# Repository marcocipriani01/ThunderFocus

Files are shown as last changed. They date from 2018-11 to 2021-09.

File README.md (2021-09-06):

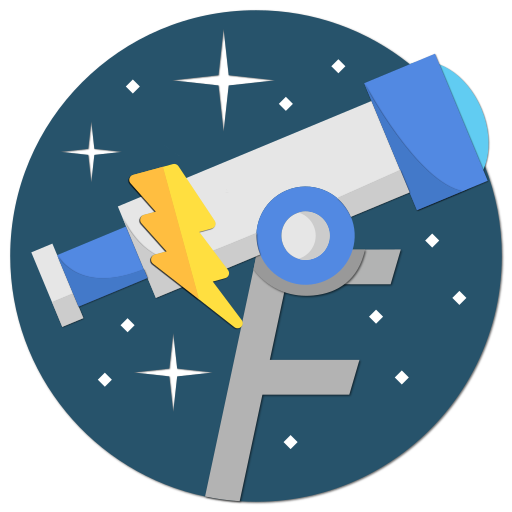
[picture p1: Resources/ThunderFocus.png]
ThunderFocus logo


# ThunderFocus

ThunderFocus is an open-source telescope focuser developed by Marco Cipriani. The source code is available on [GitHub](https://github.com/marcocipriani01/ThunderFocus) and is issued under the [GNU General Public License version 3](https://www.gnu.org/licenses/gpl-3.0.html). By using this software, you accept all the terms of its license.

## Showcase of controllers and focusers [on my website](https://marcocipriani01.github.io/projects/ThunderFocus)!

## Description of the project

ThunderFocus is an all-in-one focuser and power box (dew heater controller) designed to be fully customizable and feature-rich. It has its own control software written in Java and is both [INDI](https://indilib.org/) and [ASCOM](https://ascom-standards.org/) compatible.

The firmware can run on both Arduino and Teensy, with the only difference being the RTC support and the speed of the MCU. Thanks to the firmware configuration file, you can select only the features you need and remove the unnecessary: the control software will detect the available features and display only the options supported by the board, so you won't need to modify other files.

The user interface is platform-independent and works seamless across computers and boards like Raspberry Pi, with the only requirement being Java 15 (bundled in the Windows installer): in this way, you get the same experience no matter what OS you run. Moreover, it uses [INDIForJava](http://indiforjava.sourceforge.net/stage/index.html) for INDI/KStars compatibility and a special ASCOM driver for Windows compatibility. As a bonus, it can also be controlled using the [IPARCOS Android app](https://marcocipriani01.github.io/projects/IPARCOS) when the INDI server is enabled!

## Features

- INDI/ASCOM compatibility, cross platform interface
- Full telescope focuser control
  - Can control either one main telescope focuser or one guidescope/off-axis guider focuser
  - Backlash compensation
  - Precise micro-stepping control for pin-point stars
  - Displays the focuser position in millimeters, ticks or any unit of your liking
  - Remembers the last position
- Advanced dew heaters control, which can also turn on and off the telescope mount or other accessories.
  - Various automatic modes: temperature, dew point, humidity, sunset/sunrise
  - Manual control/override of outputs
  - Completely autonomous after configuration: can work without a PC
  - Restores the last state after power up
  - High efficiency, does not require heatsinks or cooling
- Ambient monitoring
  - Temperature, humidity, dew point
  - Graphs of the whole observing night

## Contributing to the project

I really appreciate help, feel free to fork, open issues, start pull requests...

## Installing the software

### Windows x64

Get [the latest release](https://github.com/marcocipriani01/ThunderFocus/releases) and install it. You're done!

### Debian, Ubuntu and Raspberry Pi OS

**Skip the Java installation if you already have it installed!**

Install the latest Java Development Kit available, version 16 or greater. On Ubuntu:

- `sudo apt update`
- `sudo apt install openjdk-16-jdk`

Raspberry Pi OS or Astroberry:

- Download the latest [AdoptOpenJDK](https://adoptopenjdk.net/releases.html) JRE or JDK (recommended: version 16, HotSpot JVM)
- Run `sudo mkdir /usr/java/`
- Extract the archive: `sudo tar -zxf AdoptOpenJDK.tar -C /usr/java/` (change the filename accordingly to what you downloaded)
- Run `echo 'export PATH=$PATH:/usr/java/' | sudo tee -a /etc/profile`

### macOS, Windows 32-bit and other Linux distros

Install Java version 15 or greater depending on your OS and then use the `.jar` ThunderFocus release. Someday I will add a macOS installer...

## Using the control software

Coming soon...

## The electronics

I created several circuits for ThunderFocus, all sharing more or less the same functionalities:

1. The prototype I use on my own telescope (not in this repository).
2. A Teensy 4 "overkill" board, with RTC and dual focuser support, not yet implemented in software. The PCB also includes a flip-flap circuit for [my other project](https://github.com/marcocipriani01/ArduinoFlatBox).
3. The **recommended Arduino Nano PCB**, which supports:
   - One focuser (bipolar motor)
   - Hand controller
   - Two PWM outputs and one digital for dew heaters and telescope mount power (with relay) respectively.
   - I2C RTC clock predisposition, to be implemented in software
   - Protection against over-current and reverse polarity

If you want to replicate this project, please build the third PCB. You can use the included CAM job to generate the gerber files and order them using services like [JLCPCB](https://jlcpcb.com/). The board is designed to be cut (following a line on the silkscreen) if you don't want the output controller: in this way, you can order 5 identical PCBs (the minimum on JLCPCB) and choose which one to cut and which not to. Maybe give the remaining boards to your friends and avoid wastes!

Building the board is an easy job, just add the components you see in the schematics. For reference, here's the list of what you need:

| Number | Component |
|---|:---:|
| C1 |  100uF electrolytic capacitor |
| C2 | 0.33uF electrolytic capacitor |
| C3 |  0.1uF electrolytic capacitor |
| C4 |  47uF electrolytic capacitor  |
| C5 |  100uF electrolytic capacitor |
| CNx |  2.1x5.5mm barrel plug socket |
| D1 | 1N4004 diode |
| D2 | 1N4004 diode |
| DRV1 | DRV8825 stepper driver |
| F1 | 5x20 fuse holder |
| IC1 | LM7805 linear regulator |
| J2 | RJ11/RJ12 female connector  |
| K1 | 12V relay |
| LED1 | 5mm red LED |
| Q2 | IRF540 N-channel MOSFET |
| Q3 | IRF540 N-channel MOSFET |
| Q5 | BC547 NPN transistor |
| R1 | 330 ohm resistor |
| R2 | 1K resistor |
| R3 | 4.7K resistor |
| R4 | 4.7K resistor |
| R5 | 10K resistor |
| U1 | Arduino Nano board |

## 3D-printed brackets

At the moment, the only bracket in the repository is for the Sky-Watcher 200 f/5 newtonian (2017 model, newer ones may be different) and uses a circular connector. I'm looking forward to add new 3D models with the right connector - the RJ11. Feel free to submit yours using pull requests!

## The stepper motor

The firmware is pretty much motor/driver-agnostic. Just make sure to select the right driver type in the configuration files (`DRIVER_POLOLU` if you're using the Arduino Nano PCB). On my newtonian OTA, which has a crayford focuser and only moves a DSLR, I'm using a small NEMA 11 stepper motor. My recommendation is to use a geared (1:4 ~ 1:14) stepper if you're attaching the motor directly to the focuser axis or a direct stepper if on the knob of a dual-speed focuser. Use properly sized timing belt and pulley or a shaft coupler to connect the motor to the focuser.

## Development

### Building the firmware

1. Install [Visual Studio Code](https://code.visualstudio.com/) and the [PlatformIO](https://platformio.org/install/ide?install=vscode) extension
2. Install the Arduino or Teensy core in the PlatformIO boards manager
3. Open the `ThunderFocus-firmware` folder inside VS Code
4. Select the PlatformIO Project Environment (`nanoatmega328` or `teensy40`) from the status bar, or add a custom one in `platformio.ini`
5. Open `src/config.h` and enable **one and only one** of the following lines (according to the PCB you built):
   - `#include "boards/arduino_nano_pcb.h"`
   - `#include "boards/teensy_max_pcb.h"`
6. Open the configuration file you enabled and make the appropriate changes (comments in the file will guide you)
   - Select the pins according to your circuit
   - Enable or disable features
   - Eventual errors or incompatible combinations of features will stop the compilation
7. Done! Upload the firmware

### Building the control software `jar` files

1. Install a [Java Development Kit](https://www.oracle.com/java/technologies/javase-downloads.html), version 15 or greater
2. Install [IntelliJ IDEA community](https://www.jetbrains.com/idea/)
3. Open `ThunderFocus-GUI` inside IntelliJ
4. Just run the only configuration in the project, it will build the artifacts for you and place them in the right places

### Creating the Windows installer

Requires the `jar` files. Make sure to follow the previous step.

1. Install [Inno Setup](https://jrsoftware.org/isinfo.php) and [Visual Studio](https://visualstudio.microsoft.com/it/) with Visual Basic .NET support
2. Open `ThunderFocusASCOM` inside Visual Studio
3. Compile the _Release_ configuration (do not run it)
4. Extract a copy of the [AdoptOpenJDK](https://adoptopenjdk.net/releases.html) in the `JRE-bundle` folder
    - Recommended: _OpenJDK 15_ with _HotSpot VM_, Windows x64
5. Open `InnoSetup.iss` and make the necessary changes to the file:
    - Replace `D:\ThunderFocus\` with the path to the ThunderFocus repository in your computer
6. Compile and run the Inno Setup file: it will create the Windows installer in the `Installers` folder

### Creating the Debian package

Requires the `jar` files and a Debian installation with `dpkg-deb`. Note: the Debian package will not include a bundled JDK. Make sure to install it and make the necessary changes to the `PATH` env variable.

1. Run `cd ThunderFocus-GUI/deb-builder`
2. `./build.sh` (requires `root` access to set the appropriate permissions)
3. You're done, the installer will be located in the usual `Installers` folder

## Used libraries

- [OpenJDK 15](https://openjdk.java.net/) by Oracle, [GPL v2 license with linking exception](https://openjdk.java.net/legal/gplv2+ce.html)
- [AdoptOpenJDK builds](https://adoptopenjdk.net/index.html) with HotSpot VM, by AdoptOpenJDK, [Apache 2.0 license](https://www.apache.org/licenses/LICENSE-2.0.html)
- [INDIForJava](https://indiforjava.github.io/) by Marco Cipriani, Sergio Alonso and Richard van Nieuwenhoven, [LGPL v3 license](https://github.com/INDIForJava/INDIForJava-core/blob/main/LICENSE.txt)
- [ASCOM .NET libraries](https://www.ascom-standards.org/) by The ASCOM Initiative, [ASCOM Open Source License](https://github.com/ASCOMInitiative/ASCOMPlatform/blob/master/LICENSE.txt)
- [jssc](https://github.com/java-native/jssc) by java-native and scream3r, [LGPL v3 license](https://github.com/java-native/jssc/blob/master/LICENSE.txt)
- [FlatLaf](https://github.com/JFormDesigner/FlatLaf/) by JFormDesigner, [Apache 2.0 license](https://github.com/JFormDesigner/FlatLaf/blob/master/LICENSE)
- [Gson](https://github.com/google/gson) by Google, [Apache 2.0 license](https://github.com/google/gson/blob/master/LICENSE)
- [Material icons](https://material.io/resources/icons/) by Google, [Apache 2.0 license](https://www.apache.org/licenses/LICENSE-2.0.html)
- [Arduino Core APIs](https://github.com/arduino/Arduino) by Arduino, [LGPL v3 license](https://github.com/arduino/Arduino/blob/master/license.txt)
- [AccelStepper](https://www.airspayce.com/mikem/arduino/AccelStepper/) by Mike McCauley (with modifications), [GPL v3 license](https://www.gnu.org/licenses/gpl-3.0.html)
- [Arduino Time Library](https://github.com/PaulStoffregen/Time) by Michael Margolis, [LGPL v2.1 license](https://www.gnu.org/licenses/old-licenses/lgpl-2.1.html)
- [SolarPosition library](https://github.com/KenWillmott/SolarPosition) by Ken Willmott
  - Based on [_Arduino Uno and Solar Position Calculations_](http://www.instesre.org/ArduinoDocuments.htm), © David R. Brooks, issued under the [Creative Commons Attribution-NonCommercial-NoDerivatives 4.0 International License](https://creativecommons.org/licenses/by-nc-nd/4.0/)
  - Uses equations from the book [_Astronomical Algorithms_ by Jean Meeus](https://www.willbell.com/math/mc1.HTM), published by Willmann-Bell, Inc., Richmond, VA
- [DHT sensor library](https://github.com/adafruit/DHT-sensor-library) by Adafruit, [MIT license](https://github.com/adafruit/DHT-sensor-library/blob/master/license.txt)
- [Telescope icon](https://www.flaticon.com/free-icon/telescope_547425?term=telescope&page=1&position=9&related_item_id=547425) by Freepik, [Flaticon license](https://www.freepikcompany.com/legal#nav-flaticon)

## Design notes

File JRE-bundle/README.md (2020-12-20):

ThunderFocus logo

# ThunderFocus

ThunderFocus is an open-source telescope focuser developed by Marco Cipriani. It has its own contorl software written in Java, can be integrated into an [INDI](https://indilib.org/) server and has an ASCOM driver. The source code is available on [GitHub](https://github.com/marcocipriani01/ThunderFocus) and is issued under the [GNU General Public License version 3](https://www.gnu.org/licenses/gpl-3.0.html). By using this software, you accept all the terms of its license.

## Used libraries

- [OpenJDK 14](https://openjdk.java.net/) by Oracle, [GPL v2 license with linking exception](https://openjdk.java.net/legal/gplv2+ce.html)
- [AdoptOpenJDK builds](https://adoptopenjdk.net/index.html) with HotSpot VM, by AdoptOpenJDK, [Apache 2.0 license](https://www.apache.org/licenses/LICENSE-2.0.html)
- [INDIForJava](http://indiforjava.sourceforge.net/stage/index.html) by Sergio Alonso and Richard van Nieuwenhoven, [LGPL v3 license](http://indiforjava.sourceforge.net/stage/license.html)
- [ASCOM .NET libraries](https://www.ascom-standards.org/) by The ASCOM Initiative, [ASCOM Open Source License](https://github.com/ASCOMInitiative/ASCOMPlatform/blob/master/LICENSE.txt)
- [jssc](https://github.com/java-native/jssc) by java-native and scream3r, [LGPL v3 license](https://github.com/java-native/jssc/blob/master/LICENSE.txt)
- [FlatLaf](https://github.com/JFormDesigner/FlatLaf/) by JFormDesigner, [Apache 2.0 license](https://github.com/JFormDesigner/FlatLaf/blob/master/LICENSE)
- [Gson](https://github.com/google/gson) by Google, [Apache 2.0 license](https://github.com/google/gson/blob/master/LICENSE)
- [Material icons](https://material.io/resources/icons/) by Google, [Apache 2.0 license](https://www.apache.org/licenses/LICENSE-2.0.html)
- [Arduino Core APIs](https://github.com/arduino/Arduino) by Arduino, [LGPL v3 license](https://github.com/arduino/Arduino/blob/master/license.txt)
- [AccelStepper](https://www.airspayce.com/mikem/arduino/AccelStepper/) by Mike McCauley (with modifications), [GPL v3 license](https://www.gnu.org/licenses/gpl-3.0.html)
- [Arduino Time Library](https://github.com/PaulStoffregen/Time) by Michael Margolis, [LGPL v2.1 license](https://www.gnu.org/licenses/old-licenses/lgpl-2.1.html)
- [SolarPosition library](https://github.com/KenWillmott/SolarPosition) by Ken Willmott
  - Based on [_Arduino Uno and Solar Position Calculations_](http://www.instesre.org/ArduinoDocuments.htm), © David R. Brooks, issued under the [Creative Commons Attribution-NonCommercial-NoDerivatives 4.0 International License](https://creativecommons.org/licenses/by-nc-nd/4.0/)
  - Uses equations from the book [_Astronomical Algorithms_ by Jean Meeus](https://www.willbell.com/math/mc1.HTM), published by Willmann-Bell, Inc., Richmond, VA
- [DHT sensor library](https://github.com/adafruit/DHT-sensor-library) by Adafruit, [MIT license](https://github.com/adafruit/DHT-sensor-library/blob/master/license.txt)
- [Telescope icon](https://www.flaticon.com/free-icon/telescope_547425?term=telescope&page=1&position=9&related_item_id=547425) by Freepik, [Flaticon license](https://www.freepikcompany.com/legal#nav-flaticon)

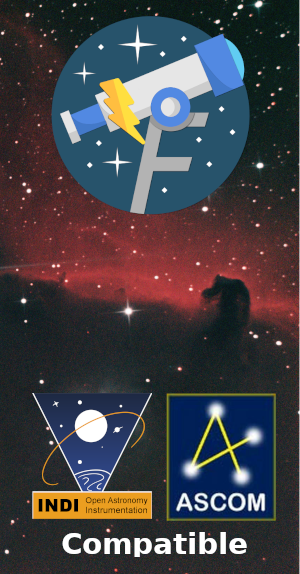
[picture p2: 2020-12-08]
WizardImage.bmp

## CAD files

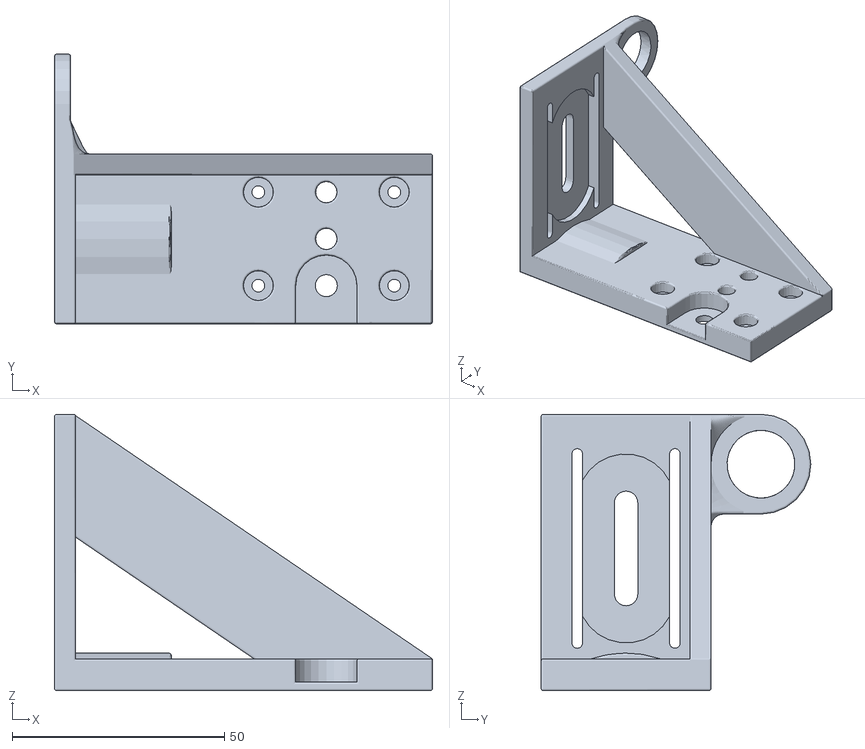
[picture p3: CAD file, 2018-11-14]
Motor brackets/SkyWatcher Dual-Speed Crayford/STL.stl
89.0 x 63.5 x 65.1

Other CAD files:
Motor brackets/SkyWatcher Dual-Speed Crayford/AutoCAD.dwg

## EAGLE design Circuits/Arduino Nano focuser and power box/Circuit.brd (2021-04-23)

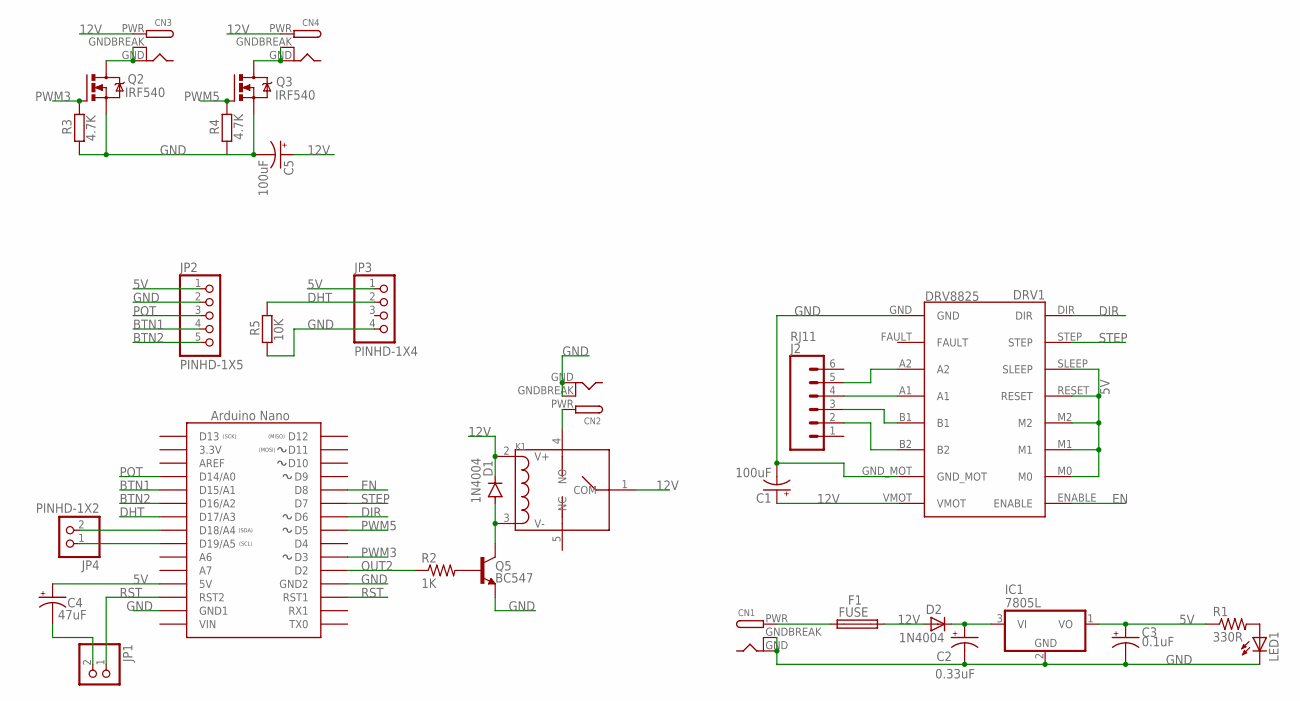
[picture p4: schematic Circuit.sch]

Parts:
C1, C5: 100uF; E2,5-6
C2: 0.33uF; E2-5
C3: 0.1uF; E2-5
C4: 47uF; E2,5-6
CN1, CN2, CN3, CN4: DCBARRELPTH; DCJACK_2MM_PTH
D1, D2: 1N4004; DO41-10
DRV1: DRV8825
F1: FUSE; SH22,5
IC1: 7805L; TO92
J2: RJ11; RJ11-6
JP1, JP4: PINHD-1X2; 1X02
JP2: PINHD-1X5; 1X05
JP3: PINHD-1X4; 1X04
K1: RELAY-HLS8L-DC5V-S-CHLS8L-DC5V-S-C; REY5-19.0X15.0X15.0MM
LED1: LED5MM
Q2, Q3: IRF540; TO220BV
Q5: BC547; TO-92
R1: 330R; 0204/7
R2: 1K; 0204/7
R3, R4: 4.7K; 0204/5
R5: 10K; 0204/5
U$1: NANO

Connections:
5V: C3.+, C4.+, DRV1.M0, DRV1.M1, DRV1.M2, DRV1.RESET, DRV1.SLEEP, IC1.1 (VO), JP2.1, JP3.1, R1.1, U$1.5V
12V: C1.+, C5.+, CN3.PWR, CN4.PWR, D1.C, D2.A, DRV1.VMOT, F1.2, K1.1 (COM), K1.2 (V+)
BTN1: JP2.4, U$1.A1 (D15/A1)
BTN2: JP2.5, U$1.A2 (D16/A2)
DHT: JP3.2, R5.2, U$1.A3 (D17/A3)
DIR: DRV1.DIR, U$1.D6
EN: DRV1.ENABLE, U$1.D8
GND: C1.-, C2.-, C3.-, C5.-, CN1.GND, CN1.GNDBREAK, CN2.GND, CN2.GNDBREAK, DRV1.GND, DRV1.GND_MOT, IC1.2 (GND), JP2.2, JP3.4, LED1.K (C), Q2.S, Q3.S, Q5.1 (E), R3.1, R4.1, R5.1, U$1.GND (GND1), U$1.GND1 (GND2)
unnamed: LED1.A, R1.2
unnamed: Q5.2 (B), R2.2
unnamed: CN2.PWR, K1.4 (NO)
unnamed: JP4.2, U$1.A4 (D18/A4)
unnamed: DRV1.A1, J2.4
unnamed: D1.A, K1.3 (V-), Q5.3 (C)
unnamed: JP4.1, U$1.A5 (D19/A5)
unnamed: C4.-, JP1.2
unnamed: DRV1.B2, J2.2
unnamed: DRV1.B1, J2.3
unnamed: DRV1.A2, J2.5
unnamed: CN1.PWR, F1.1
unnamed: CN3.GND, CN3.GNDBREAK, Q2.D
unnamed: CN4.GND, CN4.GNDBREAK, Q3.D
unnamed: C2.+, D2.C, IC1.3 (VI)
OUT2: R2.1, U$1.D2
POT: JP2.3, U$1.A0 (D14/A0)
PWM3: Q2.G, R3.2, U$1.D3
PWM5: Q3.G, R4.2, U$1.D5
RST: JP1.1, U$1.RST (RST2), U$1.RST1
STEP: DRV1.STEP, U$1.D7

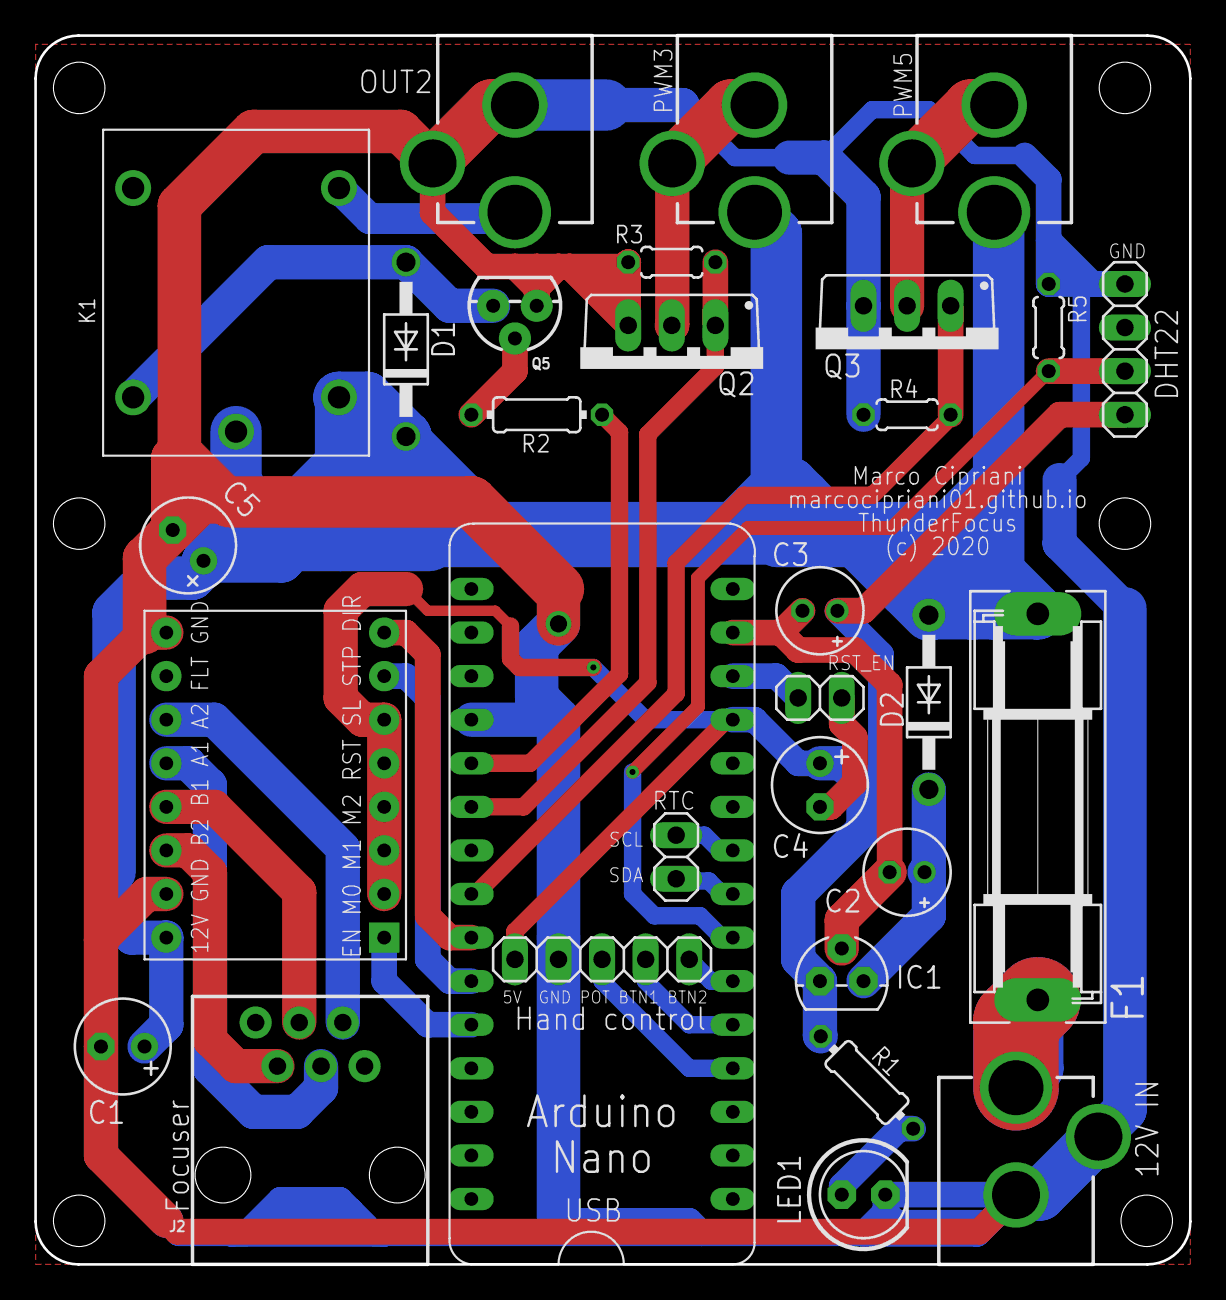
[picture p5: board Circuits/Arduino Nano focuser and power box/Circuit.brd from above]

Board: 2 copper layers, 67.3 x 71.6 mm, 30 parts (0 on the bottom side), 29 nets.

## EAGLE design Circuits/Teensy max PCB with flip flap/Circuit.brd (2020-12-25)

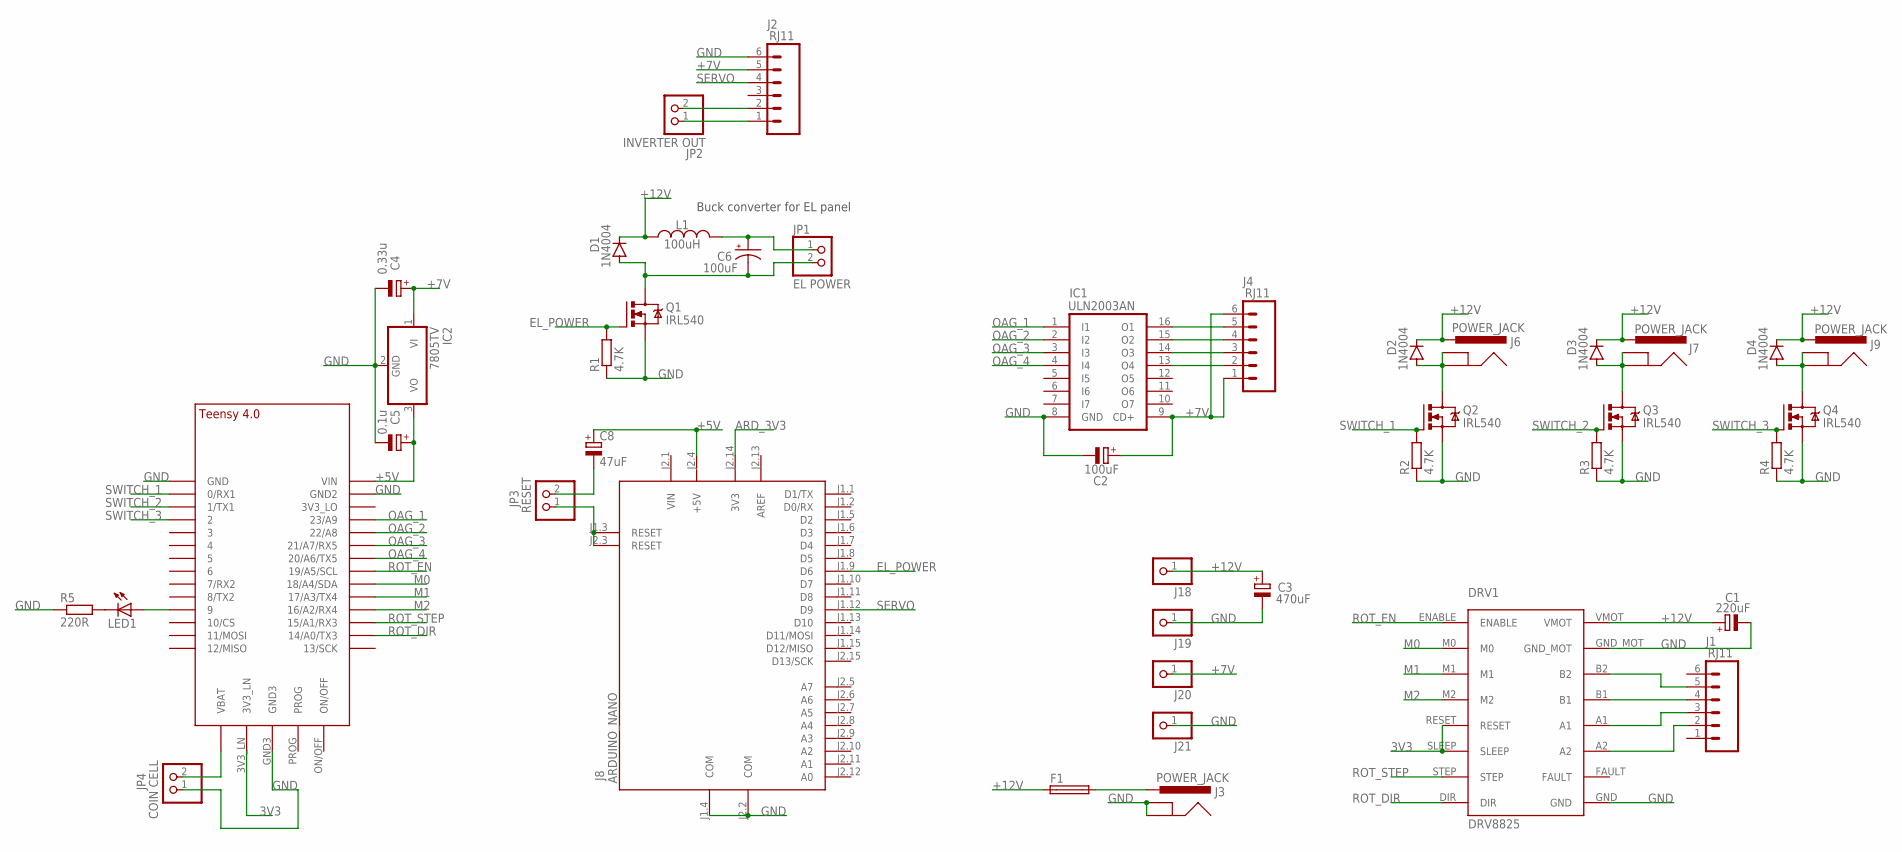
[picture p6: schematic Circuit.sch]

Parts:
C1: 220uF; E3,5-8
C2: 100uF; E2,5-6
C3: 470uF; E3,5-8
C4: 0.33u; E1,8-4
C5: 0.1u; E1,8-4
C6: 100uF; E2,5-7
C8: 47uF; E2,5-6E
D1, D2, D3, D4: 1N4004; DO41-10
DRV1: DRV8825
F1: SH22,5
IC1: ULN2003AN; DIL16
IC2: 7805TV; TO220V
J1, J2, J4: RJ11; RJ11-6
J3, J6, J7, J9: POWER_JACK; POWER_JACK_PTH
J8: ARDUINO_NANO; ARDUINO_NANO2
J18, J19, J20, J21: PINHD-1X1; 1X01
JP1: EL POWER; 1X02
JP2: INVERTER OUT; 1X02
JP3: RESET; 1X02
JP4: COIN CELL; 1X02
L1: 100uH; 6000-XXXX-RC
LED1: LED3MM
Q1, Q2, Q3, Q4: IRL540; TO220BV
R1, R2, R3, R4: 4.7K; 0204/7
R5: 220R; 0204/5
U$1: TEENSY_4.0-BASIC

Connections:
3V3: DRV1.RESET, DRV1.SLEEP, U$1.3V3_LN
+5V: C5.+, C8.+, IC2.3 (VO), J8.J2.4 (+5V), U$1.VIN
+7V: C2.+, C4.+, IC1.9 (CD+), IC2.1 (VI), J2.5, J4.1, J4.6, J20.1
+12V: C1.+, C3.+, D1.C, D2.C, D3.C, D4.C, DRV1.VMOT, F1.1, J6.PWR, J7.PWR, J9.PWR, J18.1, L1.1
ARD_3V3: J8.J2.14 (3V3)
AREF: J8.J2.13 (AREF)
EL_POWER: J8.J1.9 (D6), Q1.G, R1.2
GND: C1.-, C2.-, C3.-, C4.-, C5.-, DRV1.GND, DRV1.GND_MOT, IC1.8 (GND), IC2.2 (GND), J2.6, J3.GND, J3.GNDBREAK, J8.J1.4 (COM), J8.J2.2 (COM), J19.1, J21.1, JP4.1, Q1.S, Q2.S, Q3.S, Q4.S, R1.1, R2.1, R3.1, R4.1, R5.1, U$1.GND, U$1.GND2, U$1.GND3
M0: DRV1.M0, U$1.18/A4/SDA
M1: DRV1.M1, U$1.17/A3 (17/A3/TX4)
M2: DRV1.M2, U$1.16/A2 (16/A2/RX4)
unnamed: DRV1.B1, J1.4
unnamed: D3.A, J7.GND, J7.GNDBREAK, Q3.D
unnamed: C6.-, D1.A, JP1.2, Q1.D
unnamed: D4.A, J9.GND, J9.GNDBREAK, Q4.D
unnamed: D2.A, J6.GND, J6.GNDBREAK, Q2.D
unnamed: DRV1.B2, J1.5
unnamed: IC1.16 (O1), J4.5
unnamed: DRV1.A1, J1.3
unnamed: DRV1.A2, J1.2
unnamed: LED1.A, U$1.9/CS (9)
unnamed: LED1.K (C), R5.2
unnamed: C6.+, JP1.1, L1.2
unnamed: J2.1, JP2.1
unnamed: J2.2, JP2.2
unnamed: JP4.2, U$1.VBAT\ (VBAT)
unnamed: IC1.15 (O2), J4.4
unnamed: IC1.14 (O3), J4.3
unnamed: IC1.13 (O4), J4.2
unnamed: J8.J1.3 (RESET), J8.J2.3 (RESET), JP3.1
unnamed: C8.-, JP3.2
unnamed: F1.2, J3.PWR
OAG_1: IC1.1 (I1), U$1.23/A9
OAG_2: IC1.2 (I2), U$1.22/A8
OAG_3: IC1.3 (I3), U$1.21/A7 (21/A7/RX5)
OAG_4: IC1.4 (I4), U$1.20/A6 (20/A6/TX5)
ROT_DIR: DRV1.DIR, U$1.14/A0 (14/A0/TX3)
ROT_EN: DRV1.ENABLE, U$1.19/A5/SCL
ROT_STEP: DRV1.STEP, U$1.15/A1 (15/A1/RX3)
SERVO: J2.4, J8.J1.12 (D9)
SWITCH_1: Q2.G, R2.2, U$1.0/RX (0/RX1)
SWITCH_2: Q3.G, R3.2, U$1.1/TX (1/TX1)
SWITCH_3: Q4.G, R4.2, U$1.2
VIN: J8.J2.1 (VIN)

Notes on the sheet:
Buck converter for EL panel

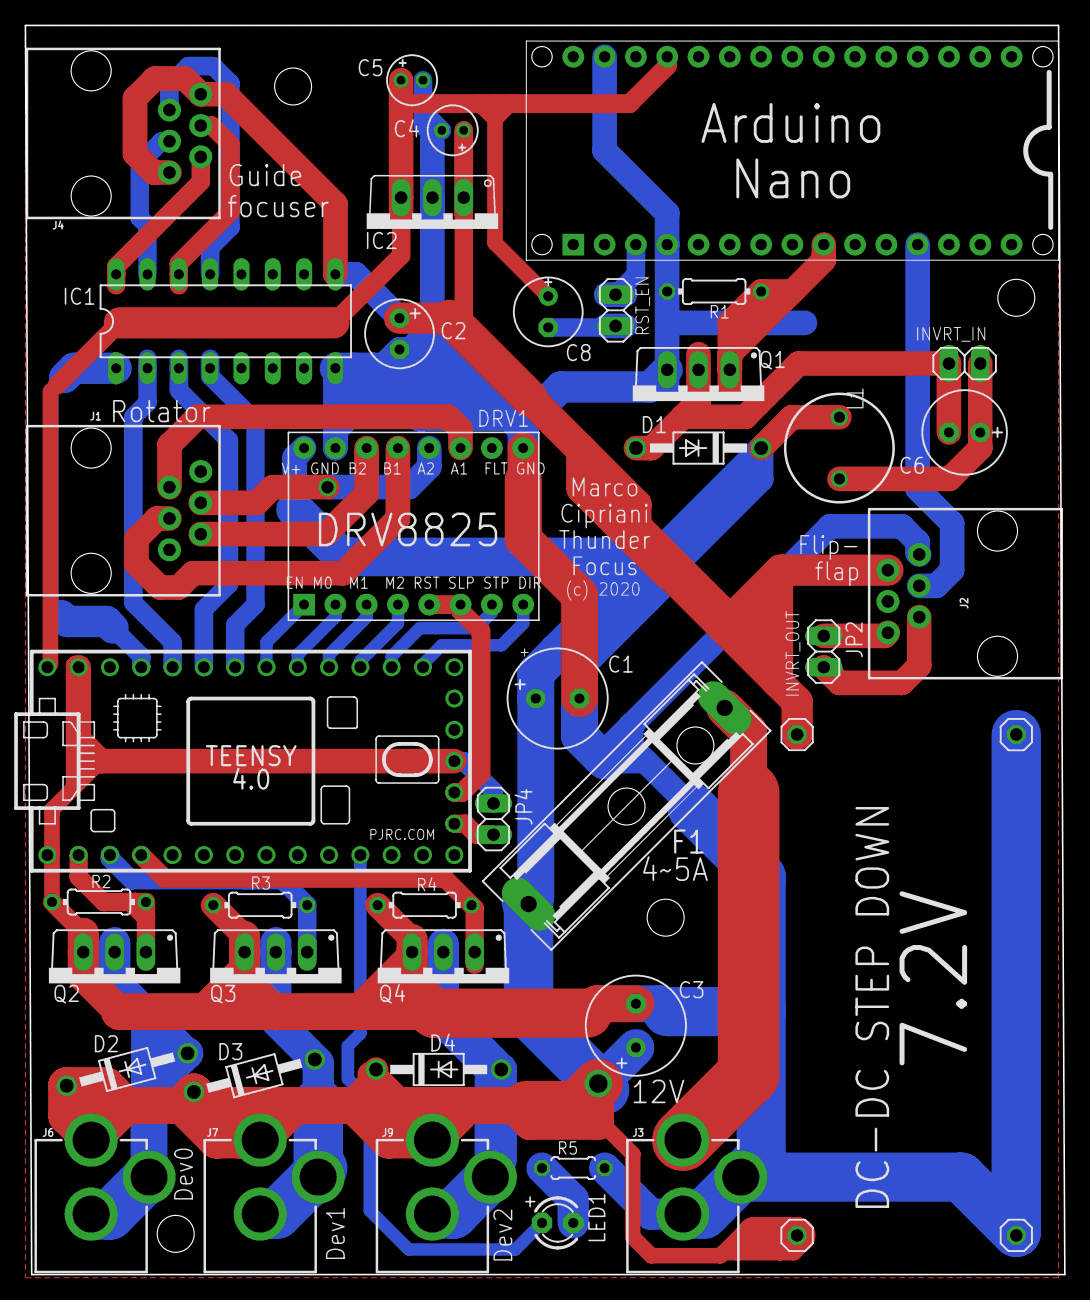
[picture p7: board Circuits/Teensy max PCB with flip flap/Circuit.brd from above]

Board: 2 copper layers, 84.3 x 101.3 mm, 43 parts (0 on the bottom side), 41 nets.

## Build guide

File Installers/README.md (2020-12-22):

# Installers

Inno setup and the Debian package generator (`../ThunderFocus-GUI/deb-builder/build.sh`) will output their installers here. Please do not remove this directory. Further information about the building process in the main README file.

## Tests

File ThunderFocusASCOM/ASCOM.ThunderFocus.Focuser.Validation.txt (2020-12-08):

Conform Report Hash (V1): 85033BAF39FFAEAFA70A7C655CA39493E24480A7E5FDB8E9913CAC063C87F26779253E530BD7F4111332175D480E95F0647E417AD477A73DC9F48CAA749FE82E

ConformanceCheck ASCOM Device Conformance Checker Version 6.5.7500.22515, Build time: 14/07/2020 13:30:30
ConformanceCheck Running on: ASCOM Platform 6.5 SP1 - RC1 6.5.1.3174
 
ConformanceCheck Driver ProgID: ASCOM.ThunderFocus.Focuser
 
Error handling 
Error number for "Not Implemented" is: 80040400
Error number for "Invalid Value 1" is: 80040404
Error number for "Value Not Set 1" is: 80040402
Error number for "Value Not Set 2" is: 80040403
Error messages will not be interpreted to infer state.
 
02:04:05.969 Driver Access Checks              OK       
02:04:06.658 AccessChecks                      OK       Successfully created driver using late binding
02:04:06.877 AccessChecks                      OK       Successfully connected using late binding
02:04:06.916 AccessChecks                      INFO     The driver is a .NET object
02:04:06.921 AccessChecks                      INFO     The AssemblyQualifiedName is: ASCOM.ThunderFocus.Focuser, ASCOM.ThunderFocus.Focuser, Version=1.0.0.0, Cul
02:04:06.927 AccessChecks                      INFO     The driver implements interface: ASCOM.DeviceInterface.IFocuserV3
02:04:07.624 AccessChecks                      INFO     Device does not expose IFocuser interface
02:04:07.699 AccessChecks                      INFO     Device does not expose IFocuserV2 interface
02:04:07.981 AccessChecks                      INFO     Device exposes IFocuserV3 interface
02:04:08.090 AccessChecks                      OK       Successfully created driver using driver access toolkit
02:04:08.308 AccessChecks                      OK       Successfully connected using driver access toolkit
02:04:08.315 AccessChecks                      OK       Successfully disconnected using driver access toolkit
 
Conform is using ASCOM.DriverAccess.Focuser to get a Focuser object
02:04:08.413 ConformanceCheck                  OK       Driver instance created successfully
02:04:08.698 ConformanceCheck                  OK       Connected OK
 
Common Driver Methods 
02:04:08.752 InterfaceVersion                  OK       3
02:04:08.793 Connected                         OK       True
02:04:08.839 Description                       OK       ThunderFocus
02:04:08.886 DriverInfo                        OK       ThunderFocus ASCOM bridge v1.0
02:04:08.934 DriverVersion                     OK       1.0
02:04:08.980 Name                              OK       ThunderFocus
02:04:09.026 CommandString                     INFO     Conform cannot test the CommandString method
02:04:09.036 CommandBlind                      INFO     Conform cannot test the CommandBlind method
02:04:09.040 CommandBool                       INFO     Conform cannot test the CommandBool method
02:04:09.046 Action                            INFO     Conform cannot test the Action method
02:04:09.052 SupportedActions                  OK       Driver returned an empty action list
 
Properties 
02:04:09.208 Absolute                          OK       True
02:04:09.213 IsMoving                          OK       False
02:04:09.220 MaxStep                           OK       32767
02:04:09.228 MaxIncrement                      OK       32767
02:04:09.234 Position                          OK       10
02:04:09.242 StepSize                          OK       Optional member threw a PropertyNotImplementedException exception.
02:04:09.248 TempCompAvailable                 OK       False
02:04:09.254 TempComp Read                     OK       False
02:04:09.260 TempComp Write                    OK       Temperature compensation is not available and a PropertyNotImplementedException exception was generated as expected
02:04:09.267 Temperature                       OK       Optional member threw a PropertyNotImplementedException exception.
 
Methods 
02:04:09.319 Halt                              OK       Focuser halted OK
02:04:09.329 Move - TempComp False                      Moving to position: 3287
02:04:23.415 Move - TempComp False                      Asynchronous move found
02:04:23.422 Move - TempComp False             OK       Absolute move OK
02:04:23.438 Move - TempComp False             INFO     Returning to original position: 10
 
Conformance test complete 
 
No errors, warnings or issues found: your driver passes ASCOM validation!! 
 
Driver Hash Value: 96E94E3A97128463894F659D37967A5CA1F95505BBA23E64E50D888965E44B537B43455BF412542469771685FBE0B1FAFF7AC356676FDA15682150DEA980DE81

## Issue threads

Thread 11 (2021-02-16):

Small INDI driver bug

marcocipriani01, 2021-02-16:
Setting digital pins does not turn on the green prop light

Closed 2021-02-18.

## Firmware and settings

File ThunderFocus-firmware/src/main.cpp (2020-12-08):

/**
   Focuser & powerbox by marcocipriani01

** Version 4.2 ***
   December 2020
   Dropped MoonLite support

** Version 4.0 ***
   November 2020

 ** Version 3.0 ***
   March 2020
 */

#include "main.h"

Focuser focuser;

// Hand controller
#if FOK1_ENABLE_HC == true
HandController hc(&focuser);
#endif

#if SETTINGS_SUPPORT == true
// Settings data for EEPROM storage
struct Settings settings;
// Flag for requesting settings to be saved
boolean needToSaveSettings = false;
unsigned long lastTimeSettingsSave = 0;

void loadSettings() {
	uint8_t* dst = (uint8_t*)&settings;
	for (unsigned int i = 0; i < sizeof(Settings); i++) {
		dst[i] = EEPROM.read(i);
	}
	if (settings.marker == EEPROM_VERSION) {
		focuser.begin((boolean) settings.fok1HoldControl, settings.fok1Speed,
			settings.fok1Backlash, settings.fok1Reverse);
		if (settings.fok1Pos != 0) {
			focuser.setCurrentPos(settings.fok1Pos);
		}
#if ENABLE_DEVMAN == true
		for (uint8_t i = 0; i < getManagedPinsCount(); i++) {
			Pin pin = settings.devManPins[i];
			if (pin.autoModeEn) {
				setPinAutoMode(pin.number, true);
			} else {
				updatePin(pin.number, pin.value);
			}
		}
		setDevManAutoMode(settings.devManAutoMode);
#endif
#if TIME_CONTROL == true
		if ((!isnan(settings.worldLat)) && (!isnan(settings.worldLong))) {
			setWorldCoord(settings.worldLat, settings.worldLong);
		}
#endif
	} else {
		settings.marker = EEPROM_VERSION;
		focuser.begin();
		saveSettings();
	}
}

void saveSettings() {
	settings.marker = EEPROM_VERSION;
	settings.fok1Pos = focuser.getCurrentPos();
	settings.fok1Speed = focuser.getSpeed();
	settings.fok1HoldControl = focuser.isHoldControlEnabled();
	settings.fok1Backlash = focuser.getBacklash();
	settings.fok1Reverse = focuser.getDirReverse();
#if ENABLE_DEVMAN == true
	for (uint8_t i = 0; i < getManagedPinsCount(); i++) {
		settings.devManPins[i] = getManagedPin(i);
	}
	settings.devManAutoMode = getDevManAutoMode();
#endif
#if TIME_CONTROL == true
	settings.worldLat = getWorldLat();
	settings.worldLong = getWorldLong();
#endif
	uint8_t* dst = (uint8_t*) &settings;
	for (unsigned int i = 0; i < sizeof(Settings); ++i) {
		EEPROM.update(i, dst[i]);
	}
}
#endif

void setup() {
	// Serial port and protocol
	Serial.begin(SERIAL_SPEED);
	Serial.setTimeout(SERIAL_TIMEOUT);

#ifdef STATUS_LED
	pinMode(STATUS_LED, OUTPUT);
#if STATUS_LED_MANAGED == true
	digitalWrite(STATUS_LED, HIGH);
	delay(400);
	digitalWrite(STATUS_LED, LOW);
#else
	digitalWrite(STATUS_LED, HIGH);
#endif
#endif

#if ENABLE_DEVMAN == true
	beginDevMan();
#endif

#if SETTINGS_SUPPORT == true
	loadSettings();
#else
	focuser.begin();
#endif

#if FOK1_ENABLE_HC == true
	hc.begin();
#endif

#if defined(__AVR_ATmega32U4__)
	while (!Serial) {
		;
	}
#endif
}

void loop() {
	if (thunderFocusManage(&focuser) == FocuserState::FOCUSER_ARRIVED) {
		flagSettings();
	}

#if ENABLE_HC == true
	hc.manage();
#endif

#if SETTINGS_SUPPORT == true
	unsigned long currentTime = millis();
	if (currentTime - lastTimeSettingsSave >= SETTINGS_SAVE_DELAY) {
		if (needToSaveSettings) {
			saveSettings();
			needToSaveSettings = false;
		}
		lastTimeSettingsSave = currentTime;
	}
#endif
}

inline void flagSettings() {
#if SETTINGS_SUPPORT == true
	needToSaveSettings = true;
#endif
}

void serialEvent() {
	if (thunderFocusSerialEvent(&focuser)) {
		flagSettings();
	}
}

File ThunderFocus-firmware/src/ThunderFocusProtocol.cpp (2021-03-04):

#include "ThunderFocusProtocol.h"

FocuserState lastFok1State = FocuserState::FOCUSER_POWERSAVE;
unsigned long lastThunderFocusSerialSend = 0;
#if TEMP_HUM_SENSOR == true
unsigned long lastThunderFocusAmbientSend = 0;
#endif
#if TIME_CONTROL == true
unsigned long lastThunderFocusSunPosSend = 0;
#endif

FocuserState thunderFocusManage(Focuser *focuser) {
	FocuserState currentState = focuser->run();
	if (currentState != lastFok1State) {
		Serial.println((char) currentState);
		lastFok1State = currentState;
	}
	unsigned long currentTime = millis();
	if (currentTime - lastThunderFocusSerialSend >= THUNDERFOCUS_SEND_DELAY) {
		Serial.print("S");
		Serial.println(focuser->getCurrentPos());
		lastThunderFocusSerialSend = currentTime;
	}
#if ENABLE_DEVMAN == true
	if (devManage()) {
		thunderFocusUpdPins();
	}
#endif
#if TEMP_HUM_SENSOR == true
	ambientManage();
	if (currentTime - lastThunderFocusAmbientSend >= AUTOMATIC_DEVMAN_TIMER) {
		Serial.print("J");
		Serial.print(getTemperature(), 1);
		Serial.print(",");
		Serial.print(getHumidity(), 1);
		Serial.print(",");
		Serial.println(getDewPoint(), 1);
		lastThunderFocusAmbientSend = currentTime;
	}
#endif
#if TIME_CONTROL == true
	if (currentTime - lastThunderFocusSunPosSend >= AUTOMATIC_DEVMAN_TIMER) {
		thunderFocusUpdSunPos();
		lastThunderFocusSunPosSend = currentTime;
	}
#endif
	return currentState;
}

boolean thunderFocusSerialEvent(Focuser *focuser) {
	while (Serial.available()) {
		if (Serial.read() == '$') {
			Serial.println("LFoundCmd");
			switch (Serial.read()) {
			case 'C': {
				Serial.print("C");
				Serial.print(FIRMWARE_VERSION);
				Serial.print(",");
				Serial.print(focuser->getCurrentPos());
				Serial.print(",");
				Serial.print(focuser->getSpeed());
				Serial.print(",");
				Serial.print(focuser->isHoldControlEnabled());
				Serial.print(",");
				Serial.print(focuser->getBacklash());
				Serial.print(",");
				Serial.print(focuser->getDirReverse());
				Serial.print(",");
				Serial.print(ENABLE_DEVMAN);
#if ENABLE_DEVMAN == true
				Serial.print(",");
				Serial.print(getDevManAutoMode());
				Serial.print(",");
				for (byte i = 0; i < getManagedPinsCount(); i++) {
					Pin pin = getManagedPin(i);
					Serial.print("(");
					Serial.print(pin.number);
					Serial.print("%");
					Serial.print(pin.value);
					Serial.print("%");
					Serial.print(pin.isPwm);
					Serial.print("%");
					Serial.print(pin.autoModeEn);
					Serial.print(")");
				}
				Serial.print(",");
				Serial.print(TEMP_HUM_SENSOR);
				Serial.print(",");
				Serial.print(TIME_CONTROL);
#if TIME_CONTROL == true
				Serial.print(",");
				Serial.print(getWorldLat(), 3);
				Serial.print(",");
				Serial.print(getWorldLong(), 3);
#endif
#endif
				Serial.println();
#if TIME_CONTROL == true
				Serial.print("LStoredTime=");
				Serial.print(hour());
				Serial.print(":");
				Serial.print(minute());
				Serial.print(":");
				Serial.print(second());
				Serial.print(" ");
				Serial.print(day());
				Serial.print("/");
				Serial.print(month());
				Serial.print("/");
				Serial.print(year());
				Serial.println(" UTC");
				thunderFocusUpdSunPos();
#endif
				break;
			}

			case 'R': {
				long n = Serial.parseInt();
				Serial.print("LMove=");
				Serial.println(n);
				focuser->move(n);
				break;
			}

			case 'A': {
				long n = Serial.parseInt();
				Serial.print("LGoTo=");
				Serial.println(n);
				focuser->moveToTargetPos(n);
				break;
			}

			case 'S': {
				Serial.println(F("LStop"));
				focuser->brake();
				break;
			}

			case 'P': {
				long n = Serial.parseInt();
				Serial.print(F("LSetPos="));
				Serial.println(n);
				focuser->setCurrentPos(n);
				return true;
			}

			case 'W': {
				Serial.println(F("LSetZero"));
				focuser->setCurrentPos(0);
				return true;
			}

			case 'H': {
				boolean b = (Serial.parseInt() > 0);
				Serial.print(F("LHoldControl="));
				Serial.println(b);
				focuser->setHoldControlEnabled(b);
				return true;
			}

			case 'V': {
				long n = Serial.parseInt();
				Serial.print(F("LSpeed="));
				Serial.println(n);
				focuser->setSpeed(n);
				return true;
			}

			case 'B': {
				long n = Serial.parseInt();
				Serial.print(F("LBacklash="));
				Serial.println(n);
				focuser->setBacklash(n);
				return true;
			}

			case 'D': {
				boolean b = (Serial.parseInt() > 0);
				Serial.print(F("LDirReverse="));
				Serial.println(b);
				focuser->setDirReverse(b);
				return true;
			}

#if ENABLE_DEVMAN == true
			case 'X': {
				byte pin = Serial.parseInt();
				byte value = Serial.parseInt();
				Serial.print(F("LSetPin="));
				Serial.print(pin);
				Serial.print(F("@"));
				Serial.println(value);
				updatePin(pin, value);
				return true;
			}

			case 'K': {
				DevManAutoModes am = (DevManAutoModes) Serial.parseInt();
				Serial.print(F("LSetAutoMode="));
				Serial.println((int) am);
				if (setDevManAutoMode(am)) {
					thunderFocusUpdPins();
				}
				return true;
			}

			case 'Y': {
				byte pin = Serial.parseInt();
				boolean amEn = (Serial.parseInt() == 1);
				Serial.print(F("LSetPinAuto="));
				Serial.print(pin);
				Serial.print(F("@"));
				Serial.println(amEn);
				if (setPinAutoMode(pin, amEn)) {
					thunderFocusUpdPins();
				}
				return true;
			}
#endif

#if TIME_CONTROL == true
			case 'T': {
				unsigned long t = Serial.parseInt();
				if (t != 0) {
					setSunKeeperTime(t);
					Serial.print(F("LSetTime="));
					Serial.println(t);
				}
				long lat = Serial.parseInt();
				long lng = Serial.parseInt();
				if (lat != 0 && lng != 0) {
					setWorldCoord(((double) lat) / 1000.0, ((double) lng) / 1000.0);
					Serial.print(F("LSetWorldCoord="));
					Serial.print(lat);
					Serial.print(",");
					Serial.println(lng);
					thunderFocusUpdSunPos();
					return true;
				}
				break;
			}
#endif
			}
		}
	}
	return false;
}

#if ENABLE_DEVMAN == true
void thunderFocusUpdPins() {
	Serial.print("Y");
	Serial.print(getDevManAutoMode());
	Serial.print(",");
	for (byte i = 0; i < getManagedPinsCount(); i++) {
		Pin pin = getManagedPin(i);
		if (pin.autoModeEn) {
			Serial.print("(");
			Serial.print(pin.number);
			Serial.print("%");
			Serial.print(pin.value);
			Serial.print(")");
		}
	}
	Serial.println();
}
#endif

#if TIME_CONTROL == true
inline void thunderFocusUpdSunPos() {
	Serial.print("T");
	Serial.println(getCalculatedSunElev(), 2);
}
#endif

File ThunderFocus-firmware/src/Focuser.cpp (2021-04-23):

#include "Focuser.h"

Focuser::Focuser() :
#if FOK1_STEPPER == DRIVER_POLOLU
	stepper(AccelStepper::DRIVER, FOK1_STEP, FOK1_DIR)
#elif FOK1_STEPPER == DRIVER_ULN2003
	stepper(AccelStepper::FULL4WIRE, FOK1_IN1, FOK1_IN2, FOK1_IN3, FOK1_IN4)
#else
#error Unsupported focuser driver
#endif
{
	stepper.setAcceleration(FOK1_ACCEL);
	lastMovementTime = millis();
	powerOn = false;
	isMoving = false;
	isHcMoving = true;
}

void Focuser::begin(boolean initHoldControlEnabled,
                    uint8_t initSpeed,
                    long backlash,
					boolean reverseDir) {
	stepper.setMinPulseWidth(0);
#ifdef FOK1_EN
	stepper.setEnablePin(FOK1_EN, true);
#endif
	stepper.setDirectionInverted(reverseDir);
#ifdef FOK1_MODE0
	pinMode(FOK1_MODE0, OUTPUT);
	digitalWrite(FOK1_MODE0, HIGH);
#endif
#ifdef FOK1_MODE1
	pinMode(FOK1_MODE1, OUTPUT);
	digitalWrite(FOK1_MODE1, HIGH);
#endif
#ifdef FOK1_MODE2
	pinMode(FOK1_MODE2, OUTPUT);
	digitalWrite(FOK1_MODE2, HIGH);
#endif
	stepper.setBacklash(backlash);
	speed = initSpeed;
	applySpeed();
	holdControlEnabled = initHoldControlEnabled;
	turnOff();
}

void Focuser::begin() {
	begin(FOK1_HOLD_CONTROL, 80, 0, FOK1_DIR_INVERT);
}

void Focuser::moveToTargetPos(long newPos) {
	isHcMoving = false;
	turnOn();
	applySpeed();
	stepper.moveTo(newPos);
}

void Focuser::move(long newPos) {
	isHcMoving = false;
	turnOn();
	applySpeed();
	stepper.move(newPos);
}

long Focuser::getTargetPos() {
	return stepper.targetPosition();
}

void Focuser::brake() {
	if (isMoving) stepper.stop();
}

void Focuser::setCurrentPos(long newPos) {
	if (!isMoving) {
		stepper.setCurrentPosition(newPos);
	}
}

long Focuser::getCurrentPos() {
	return stepper.currentPosition();
}

FocuserState Focuser::run() {
	unsigned long time = millis();
	if (isMoving) {
		if (stepper.run()) {
			return FocuserState::FOCUSER_MOVING;
		} else {
			isMoving = false;
			applySpeed();
			lastMovementTime = time;
			return FocuserState::FOCUSER_ARRIVED;
		}
	}
	if (powerOn) {
		// Turn power off if active time period has passed
		if (holdControlEnabled && ((time - lastMovementTime) >= FOK1_POWER_TIMEOUT)) {
			turnOff();
		}
		return FocuserState::FOCUSER_HOLD;
	}
	return FocuserState::FOCUSER_POWERSAVE;
}

boolean Focuser::isRunning() {
	return stepper.distanceToGo() != 0;
}

void Focuser::setHoldControlEnabled(boolean holdControlEnabledNew) {
	holdControlEnabled = holdControlEnabledNew;
}

boolean Focuser::isHoldControlEnabled() {
	return holdControlEnabled;
}

boolean Focuser::isPowerOn() {
	return powerOn;
}

void Focuser::setSpeed(uint8_t speedNew) {
	speed = speedNew;
	if (!isMoving) {
		applySpeed();
	}
}

uint8_t Focuser::getSpeed() {
	return speed;
}

void Focuser::setDirReverse(boolean b) {
	stepper.setDirectionInverted(b);
}

boolean Focuser::getDirReverse() {
	return stepper.isDirectionInverted();
}

void Focuser::setBacklash(long backlash) {
	stepper.setBacklash(backlash);
}

long Focuser::getBacklash() {
	return stepper.getBacklash();
}

void Focuser::setHCSpeedInterval(unsigned int ppsMin, unsigned int ppsMax) {
	hCMinPPS = ppsMin;
	hCMaxPPS = ppsMax;
}

void Focuser::setHCMaxStepsPerPush(long maxStepsPerPushNew) {
	maxStepsPerPush = maxStepsPerPushNew;
}

void Focuser::hCMove(unsigned int analogValue, boolean reverse) {
	if (isHcMoving || !isMoving) {
		stepper.setMaxSpeed(map(analogValue, 0, 1023, hCMinPPS, hCMaxPPS));
		long steps = map(analogValue, 0, 1023, 1, maxStepsPerPush);
		turnOn();
		isHcMoving = true;
		if (reverse) {
			stepper.move(-steps);
		} else {
			stepper.move(steps);
		}
	}
}

void Focuser::applySpeed() {
	stepper.setMaxSpeed(map(speed, 0, 100, FOK1_PPS_MIN, FOK1_PPS_MAX));
}

void Focuser::turnOn() {
	stepper.enableOutputs();
	powerOn = true;
	isMoving = true;
}

void Focuser::turnOff() {
	stepper.disableOutputs();
	powerOn = false;
	isMoving = false;
}

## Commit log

2018-11-14 Inital commit
    [AutoCAD.dwg, IGS.igs, Plus.brd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]
2019-05-20 Fix launcher bug, lighter L&F
    [Main.java]
2019-05-23 Bug fixing, added italian language
    [Main.java]
2019-09-11 Bug fixing, new release
    [Main.java]
2019-09-30 Pushing the first commits for the new OpenFocuser! Experimental stuff!
    [Circuit.brd, Circuit.sch, Plus.brd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]
2020-04-17 17 apr update
    [Circuit.brd]
2020-11-21 Update README & res
    [IGS.igs]
2020-11-30 Experimental auto dew heaters
2020-12-01 Working PowerBox, automatic modes left to test
2020-12-06 Version 2.1 beta
    [Circuit.brd, Circuit.sch, Powerbox.brd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]
2020-12-07 ASCOM driver working
2020-12-08 Fix compile bugs and update installer
    [MainWindow.java, ThunderFocusProtocol.cpp]
2020-12-16 Fix bugs, improve backlash calibration
    [Focuser.cpp, MainWindow.java, teensy_max_pcb.h]
2020-12-18 Update ASCOM driver
2020-12-21 Refresh circuits
    [Circuit.brd, Circuit.sch]
2020-12-25 New circuit
    [Circuit.brd, Circuit.sch]
2020-12-30 Update files
    [Circuit.brd]
2021-01-01 Update to Java 15, fix browser bug
    [Main.java]
2021-02-18 Bug fixing, new version, updated libraries, added debug mode
    [INDIThunderFocuserDriver.java, Main.java, MainWindow.java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]
2021-02-20 Automatic powerbox apply, crash fix
    [JPowerBoxTable.java, MainWindow.java]
2021-03-04 Position calibrator
2021-09-06 2.6.0 update: using Gradle for dependency resolving, updated libraries, improved powerbox manager with new features, small optimizations.

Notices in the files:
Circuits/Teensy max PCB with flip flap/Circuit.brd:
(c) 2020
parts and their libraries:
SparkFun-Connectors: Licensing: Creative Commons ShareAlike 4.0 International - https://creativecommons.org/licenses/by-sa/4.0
